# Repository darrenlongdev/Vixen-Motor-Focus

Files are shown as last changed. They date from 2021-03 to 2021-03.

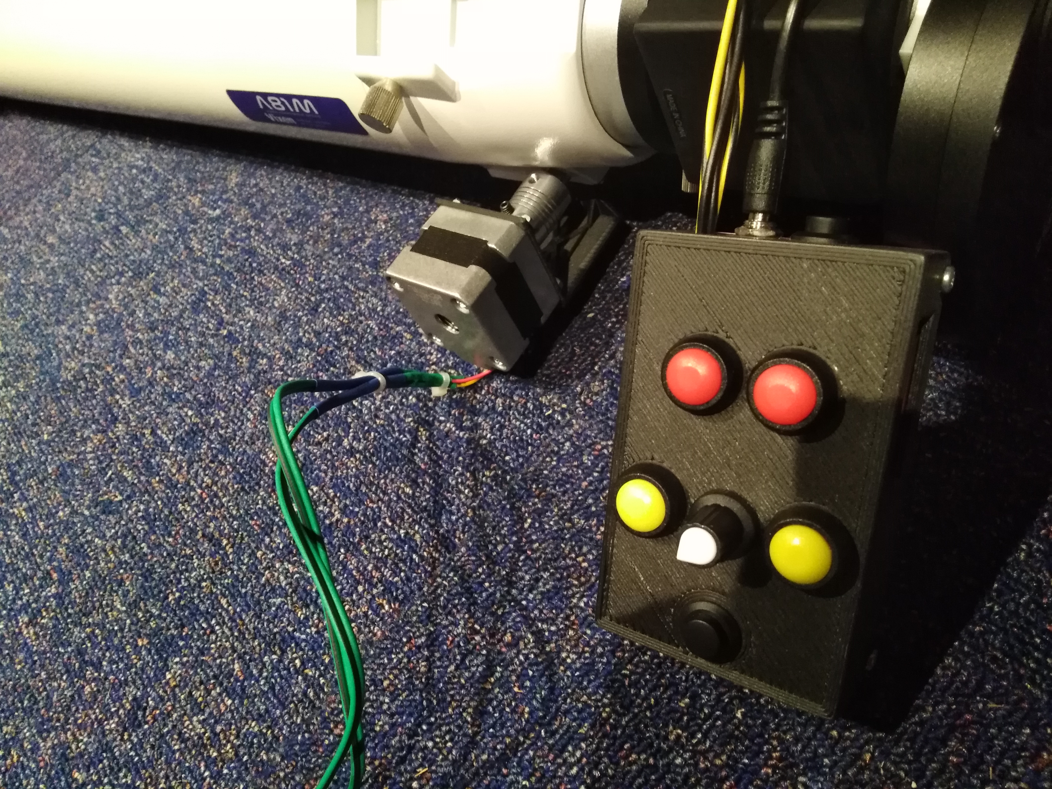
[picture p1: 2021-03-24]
images/handset.jpg

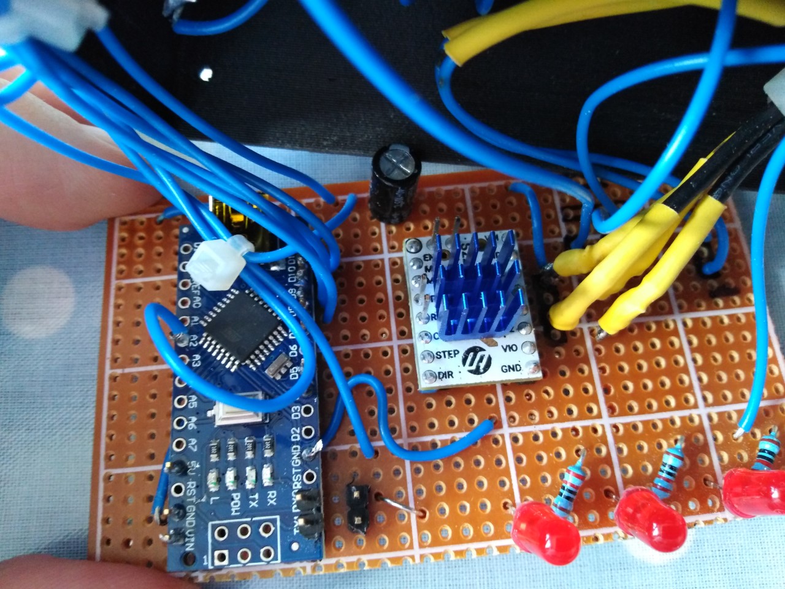
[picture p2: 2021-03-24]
images/pcb_image2.jpg

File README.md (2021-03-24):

# Vixen-Motor-Focus
Motor focuser system for Vixen 2.7" Focuser
3d files, Arduino C++ code, Schematic and reference images included in this repository.

Motor focuser system for Vixen 2.7" Focuser using easily available and 3d printed components.

Integrated red light torch to aid in setting up your equiptment whilst in dark conditions.

Nema 17 Bipolar 0.8A 26Ncm stepper motor has been used as it boasts enough torque to drive shaft without it spinning back.

TMC2209 as these enable the motor to run silently with no vibration. The EN pin is the enabler pin, the arduino can turn the TMC2209 on and off with it. Step and Dir pins allow you to step the motor and change direction.

12v 2A PSU has enough power to run the motor efficiently. Be sure to disconnect your programmer before plugging in the power!

100uf 50v Capacitor to protect parts from voltage drops and noise caused by the driver and supply power for short peaks in demand, so effectively enabling the 12V power source supply much more current for short time.

Arduino Nano is compact, incorporates a 5v voltage regulator and ample analogue / digital inputs and outputs to meet the requirement.

Push buttons for fast motion and slow motion enable simple and accurate focusing.

A potentiometer allows us to adjust the motor speed for the slow motion buttons.

The motor cannot be turned by hand when the TMC2209 is enabled, so an On/Off button for the Arduino and TMC2209 enable us to turn it off and move it by hand.

Strip board with copper tape applied to make required tracks and a drill bit to cut the required tracks makes a perfect PCB.

Programmer pins enable us to reliably program cheaper chinese Arduino's with an FTDI interface. You will have to manually press the reset button at point of upload.

Flexible Shaft Coupling (5mm to 6mm) enables you to join the motor to the focuser shaft with a little flex to account for any misalignment. Mine probably is about 1mm out so flexes a tad.

I used rubber washers to mount the motor to the bracket to soak up any vibration.

3D printed mounting bracket in 15% carbon fibre PLA to provide suitable strength. It should grip the screws for the focuser enabling you to turn them back a turn or so to allow the focuser to move freely. Be careful when taking apart the focuser, there are some washers underneath the metal plate that can easily drop into the telescope.

3D printed handset, top in 15% carbon fibre and bottom in a softer more flexible material.

In terms of licensing, Creative Commons Attribution-NonCommercial-NoDerivatives 4.0 International (CC BY-NC-ND 4.0), as I'm happy for people to redistribute it, so long as they credit myself.

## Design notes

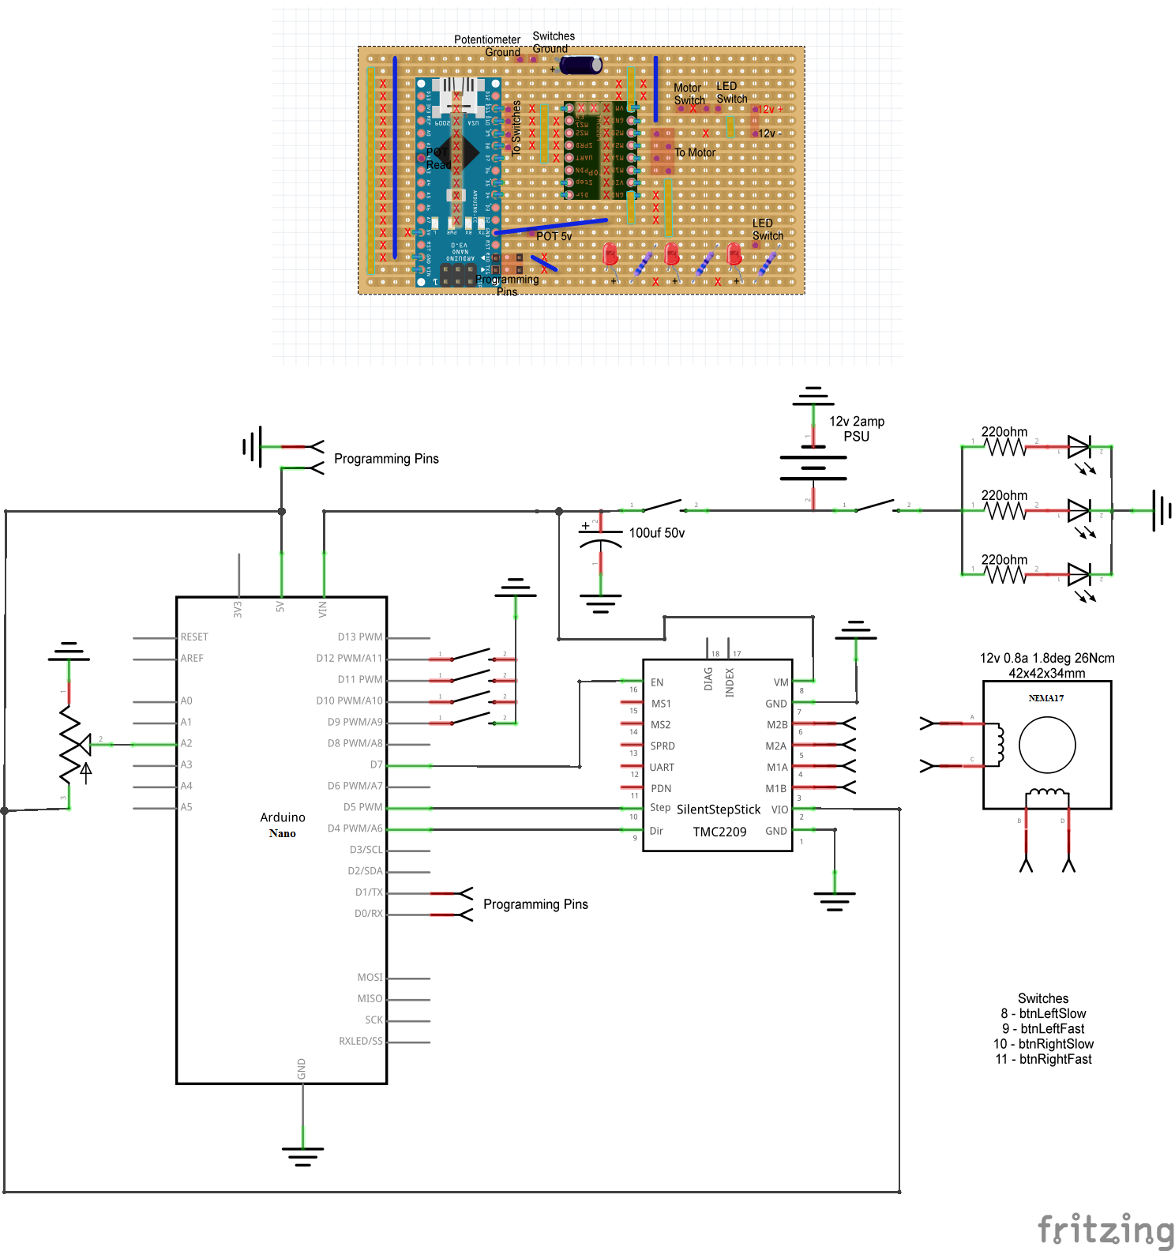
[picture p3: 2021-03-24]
schematic/pcb_and_schematic.png

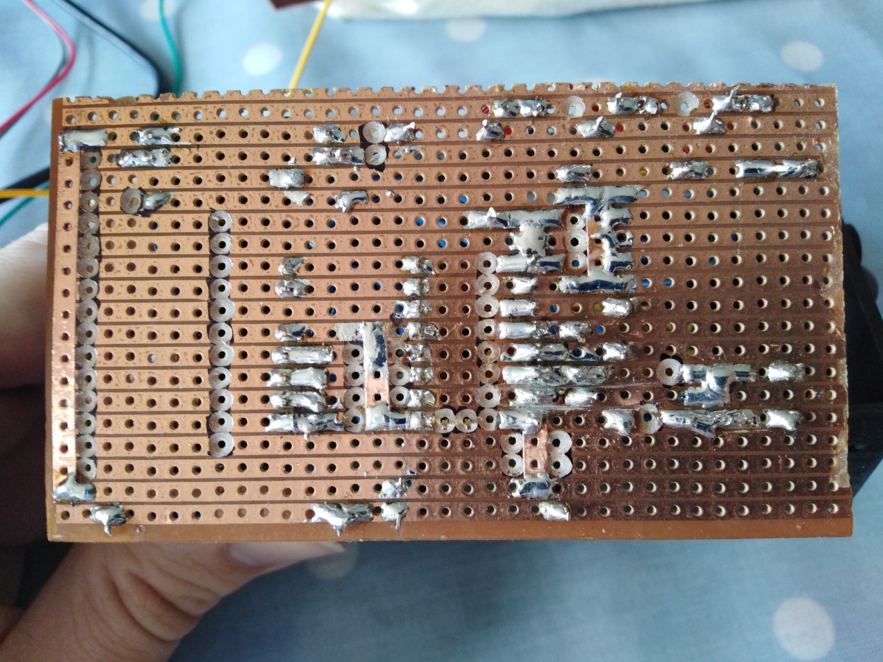
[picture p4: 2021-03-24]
images/pcb_image1.jpg

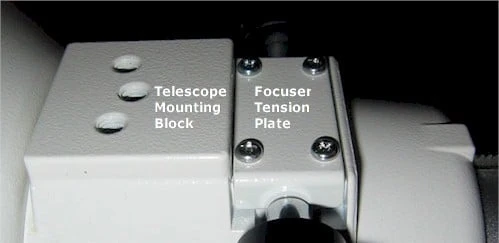
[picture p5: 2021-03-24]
images/vixen_focuser_photo.png

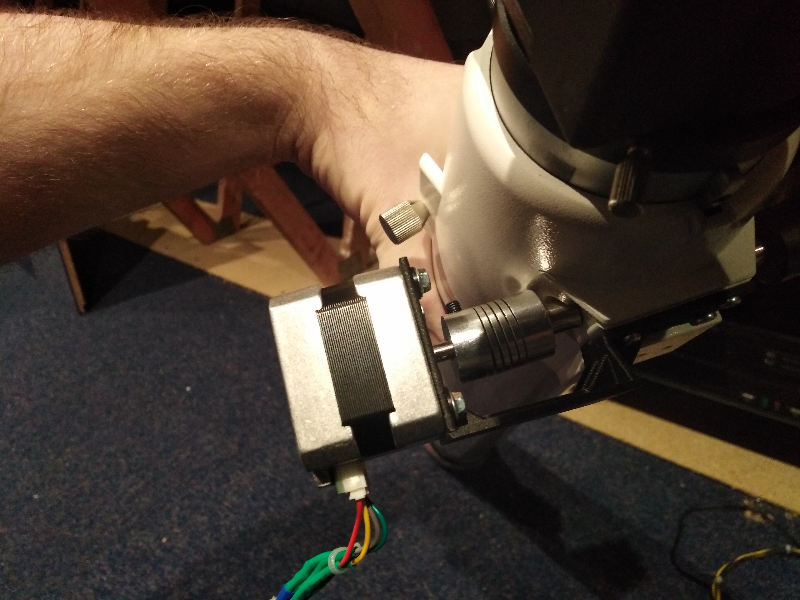
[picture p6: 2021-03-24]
images/motor_fitted.jpg

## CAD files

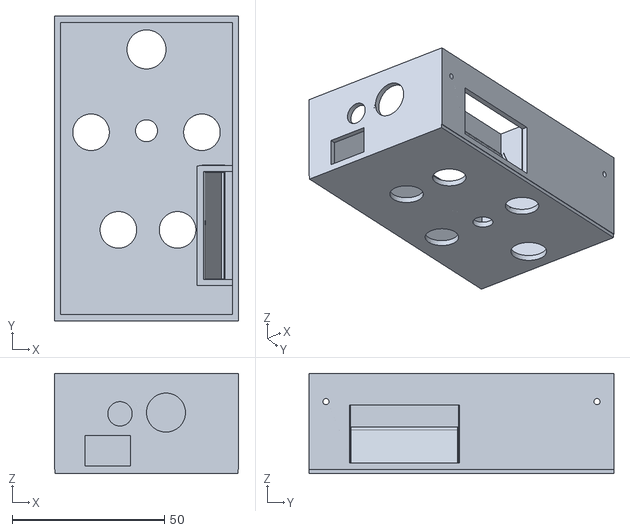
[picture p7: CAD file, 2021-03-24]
3d/handset_top_v2.stl
60.4 x 100.0 x 32.9

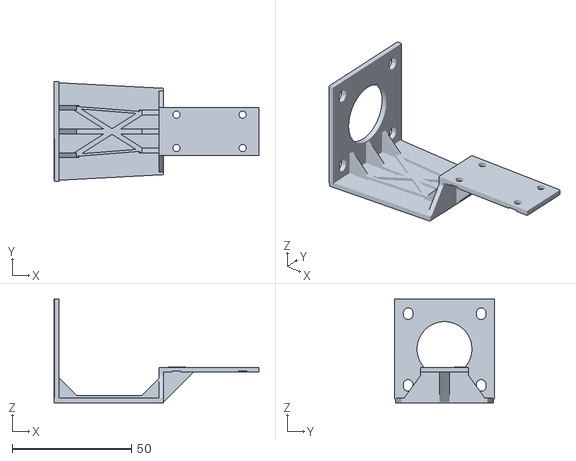
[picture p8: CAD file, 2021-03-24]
3d/bracket.stl
86.1 x 42.0 x 43.6

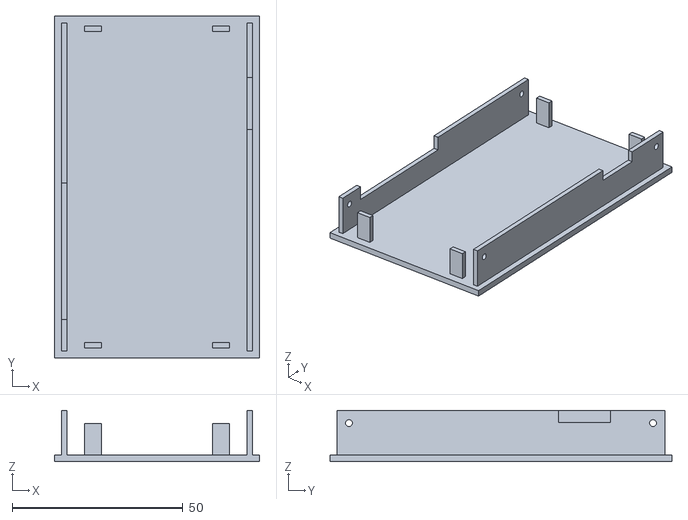
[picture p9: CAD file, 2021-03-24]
3d/handset_base.stl
60.0 x 100.0 x 15.0

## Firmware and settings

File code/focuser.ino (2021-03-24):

/**
 * Darren Long - Telescope Focuser
 */

#define DIR_PIN   4 // Direction
#define STEP_PIN  5 // Step
#define EN_PIN    7 //enable

void setup() {
  pinMode(EN_PIN, OUTPUT);
  pinMode(STEP_PIN, OUTPUT);
  pinMode(DIR_PIN, OUTPUT);
  
  pinMode(8, INPUT_PULLUP); // btnLeftSlowPin
  pinMode(9, INPUT_PULLUP); // btnLeftFastPin
  pinMode(10, INPUT_PULLUP); // btnRightSlowPin
  pinMode(11, INPUT_PULLUP); // btnRightFastPin
  
  digitalWrite(EN_PIN, LOW); //activate driver
  //digitalWrite(EN_PIN, HIGH); //disable driver
}

void loop() {

int iPot = round(map(analogRead(2), 0, 1023, 16000, 6000));

int btnLeftSlow = digitalRead(8);
int btnLeftFast = digitalRead(9);
int btnRightSlow = digitalRead(10);
int btnRightFast = digitalRead(11);

if (btnLeftSlow == LOW) { 
  digitalWrite(DIR_PIN, LOW); // Direction
    digitalWrite(STEP_PIN, HIGH);
    delayMicroseconds(960);
    digitalWrite(STEP_PIN, LOW);
    delayMicroseconds(iPot); //16000
 } 

if (btnRightSlow == LOW) { 
  digitalWrite(DIR_PIN, HIGH); // Direction
    digitalWrite(STEP_PIN, HIGH);
    delayMicroseconds(960);
    digitalWrite(STEP_PIN, LOW);
    delayMicroseconds(iPot); //16000
 } 
 
 if (btnLeftFast == LOW) { 
  digitalWrite(DIR_PIN, LOW); // Direction
    digitalWrite(STEP_PIN, HIGH);
    delayMicroseconds(960);
    digitalWrite(STEP_PIN, LOW);
    delayMicroseconds(960);
 } 

if (btnRightFast == LOW) { 
  digitalWrite(DIR_PIN, HIGH); // Direction
    digitalWrite(STEP_PIN, HIGH);
    delayMicroseconds(960);
    digitalWrite(STEP_PIN, LOW);
    delayMicroseconds(960);
 } 
 
 }
